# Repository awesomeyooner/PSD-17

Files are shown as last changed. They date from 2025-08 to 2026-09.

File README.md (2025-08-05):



# PSD-17

The PSD-21 is an FOC controller designed for stepper motors, specifically for NEMA 17 stepper motors.

Click here for the [manual](./docs/Manual.md)
## Folder Tree

```bash
.
├── esp_test_firmware # Test firmware on ESP32
│   └── firmware # PlatformIO Project
├── firmware # Main firmware (SAMD21)
├── i2c_test # I2C Master Communication Test
│   └── project  # CMake Project
├── pcb # KiCad Project
├── samd21_test_firmware # Test firmware on SAMD21
│   └── firmware # PlatformIO Project
└── README.md
```

## Hardware Details

- [NEMA 17 Motor](https://www.omc-stepperonline.com/nema-17-stepper-motor)
    - [STEPPERONLINE 23mm](https://www.amazon.com/dp/B0B93PNYCP?ref=ppx_yo2ov_dt_b_fed_asin_title&th=1)
    - [STEPPERONLINE 38mm](https://www.amazon.com/dp/B0B38GX54H?ref=ppx_yo2ov_dt_b_fed_asin_title&th=1)
- [AS5047P Magnetic Encoder](https://www.digikey.com/en/products/detail/ams-osram-usa-inc/AS5047P-ADAPTERBOARD/5452344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)
    - [Diametric Magnet](https://www.digikey.com/en/products/detail/radial-magnets-inc/9049/6030786) (6mm x 2.5mm )
- [DRV8874 DC Motor Driver](https://www.pololu.com/product/4035) (2x)
- [SAMD21 Seeed Studio Xiao](https://www.amazon.com/Seeeduino-Smallest-Microcontroller-Interfaces-Compatible/dp/B08745JBRP?th=1)

### Passive Components 

- [5V Voltage Regulator](https://www.pololu.com/product/5433?gQT=1)

## Datasheets

### AS5047P
- [Board](https://www.mouser.com/datasheet/2/588/AS5047P-TS_EK_AB_Operation-Manual_Rev.1.0-775823.pdf)
- [Chip](https://look.ams-osram.com/m/d05ee39221f9857/original/AS5047P-DS000324.pdf)

### DRV8874
- [Board](https://www.pololu.com/product/4035)
- [Chip](https://www.ti.com/lit/ds/symlink/drv8874.pdf)

### SAMD21
- [Seeed Studio Xiao](https://wiki.seeedstudio.com/Seeeduino-XIAO/)
- [SAMD21 Chip](https://ww1.microchip.com/downloads/en/DeviceDoc/SAM_D21_DA1_Family_DataSheet_DS40001882F.pdf)

### NEMA 17
- [23mm](https://www.omc-stepperonline.com/e-series-nema-17-bipolar-1-8deg-17ncm-24-07oz-in-1a-42x42x23mm-4-wires-17he08-1004s)
- [38mm](https://www.omc-stepperonline.com/e-series-nema-17-bipolar-42ncm-59-49oz-in-1-5a-42x42x38mm-4-wires-w-1m-cable-connector-17he15-1504s)

## Contact
Feel free to reach out!
- awesomeyooner@gmail.com

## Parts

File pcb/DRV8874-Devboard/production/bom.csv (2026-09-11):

Designator | Footprint | Quantity | Value | LCSC Part #
C1, C7 | 0402 | 2 | 22nF | C1532
C10 | 0603 | 1 | 10uF | C96446
C11, C14, C15, C16, C17, C18, C19, C2, C5, C8, C9 | 0402 | 11 | 100nF | C307331
C12 | 1206 | 1 | 4.7uF | C29823
C13 | 0603 | 1 | 33pF | C1663
C3, C6 | CP_Elec_10x10.5 | 2 | 330uF | C46550419
C4 | 0603 | 1 | 33nF | C21117
D1, D3, D4, D5 | LED_WS2812B-2020_PLCC4_2.0x2.0mm | 4 | WS2812B-2020 | C3646929
D2 | D_SMA | 1 | D_Schottky | C2480
J1, J5 | PinHeader_1x04_P2.54mm_Vertical | 2 | Conn_01x04_Pin
J10, J11 | PinHeader_1x06_P2.54mm_Vertical | 2 | Conn_01x06_Pin
J12, J3, J4, J6, J7, J8, J9 | PinHeader_1x03_P2.54mm_Vertical | 7 | Conn_01x03_Pin
J13, J14 | PinHeader_1x02_P2.54mm_Vertical | 2 | Conn_01x02_Pin
J2 | CONN-TH_2P-P5.08_DB128L-5.08-2P-BK-S | 1 | Screw_Terminal_01x02 | C430601
L2 | 1008 | 1 | 4u7 | C5832360
R1, R19 | 0402 | 2 | 2k2 | C25879
R10, R15, R18 | 0603 | 3 | 20k | C4184
R11 | 0603 | 1 | 124k | C22788
R12 | 0603 | 1 | 23k7 | C2933175
R13, R16 | 0603 | 2 | 15k | C22809
R14, R17 | 0603 | 2 | 75k | C23242
R2, R21, R6 | 0402 | 3 | 10k | C25744
R22, R9 | 0603 | 2 | 100k | C25803
R23 | 0402 | 1 | 470 | C25117
R3 | 0402 | 1 | 120 | C25079
R5 | 0603 | 1 | 3k | C4211
R7 | 0603 | 1 | 18k | C25810
R8 | 0603 | 1 | 510k | C23192
U1, U3 | HTSSOP-16-1EP_4.4x5mm_P0.65mm_EP3.4x5mm_Mask2.46x2.31mm | 2 | DRV8874 | C1855818
U2 | SOT-23-6 | 1 | BL9342 | C93176
U4 | SOIC-8_3.9x4.9mm_P1.27mm | 1 | SN65HVD230 | C12084
U5 | HTSSOP20_PWP_TEX | 1 | TPS16630PWPR | C1849461
U6 | SO-8_3.9x4.9mm_P1.27mm | 1 | M95320-WMN6TP | C283459
U7 | TinyThinker_HAT | 1 | TinyThinker_J1 | C1525

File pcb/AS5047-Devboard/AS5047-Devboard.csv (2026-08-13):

Comment | Designator | JLCPCB Part # | Footprint | Qty | DNP
1uF | C1 | C15849 | Capacitor_SMD:C_0603_1608Metric | 1
MountingHole | H1,H2,H3,H4 |  | MountingHole:MountingHole_3.2mm_M3 | 4 | DNP
SPI_CONN | J1 |  | Connector_PinHeader_2.54mm:PinHeader_1x06_P2.54mm_Vertical | 1 | DNP
AS5047P | U1 | C962063 | Package_SO:TSSOP-14_4.4x5mm_P0.65mm | 1

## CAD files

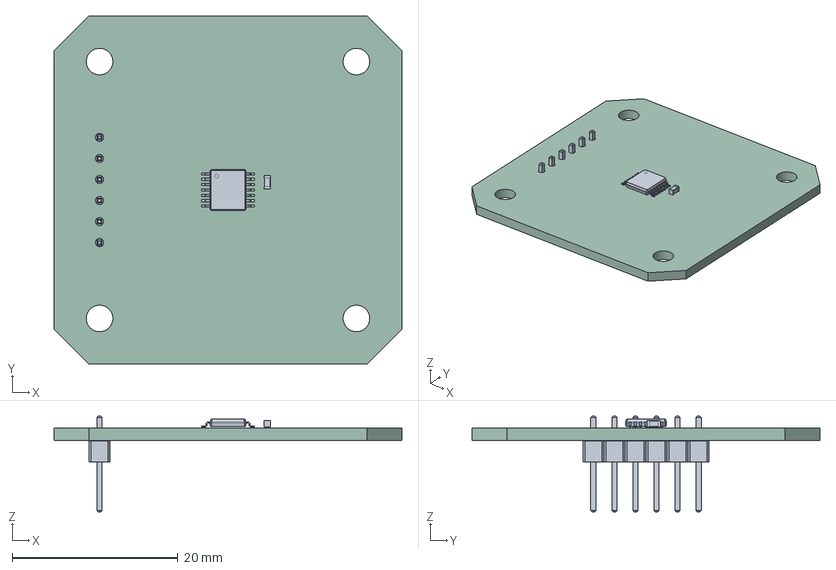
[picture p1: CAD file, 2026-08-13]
pcb/AS5047-Devboard/AS5047-Devboard.step
42.0 x 42.0 x 11.5 mm
TSSOP-14_4.4x5mm_P0.65mm
C_0603_1608Metric
PinHeader_1x06_P2.54mm_Vertical
AS5047-Devboard_PCB

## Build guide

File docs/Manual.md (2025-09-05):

# Manual for PSD 17

## I2C Communication

| Byte 1 | Byte 2... Byte N |
| --- | --- |
| Data Type | Data |

> **NOTE** Data Length is the number of bytes for the `data` section, so it does not include the first byte

### Commands 
| Data Types | Byte Value | Data Length (to send) |
| :---: | :---: | :---: |
| Disable Motor Command | 0 | 0 |
| Enable Motor Command | 1 | 0 |
| Run FOC Init | 2 | 0 |
| Target Command | 3 | 4 (float) |
| Closed Loop Velocity Command | 4 | 4 (float) |  
| Closed Loop Position Command | 5 | 4 (float) |
| Closed Loop Torque Command | 6 | 4 (float) |
| Open Loop Velocity Command | 7 | 4 (float) |
| ... | ... | ... |

### Settings 

> **NOTE** For Torque Modes, 0 is `Voltage`, 1 is `DC Current`, 2 is `FOC Current`

| Data Types | Byte Value | Data Length (to send) |
| :---: | :---: | :---: |
| Change Motor Current Limit | 121 | 4 (float) |
| Change Motor Phase Resistance | 122 | 4 (float) |
| Change Motor Voltage Alignment | 123 | 4 (float) |
| Change Motor Voltage Limit | 124 | 4 (float) |
| Change Driver Voltage Limit | 125 | 4 (float) |
| Change Supply Voltage | 126 | 4 (float) |
| Change Torque Mode | 127 | 4 (float) | 
| Velocity kP | 128 | 4 (float) |
| Velocity kI | 129 | 4 (float) |
| Velocity kD | 130 | 4 (float) |
| Position kP | 131 | 4 (float) |
| Position kI | 132 | 4 (float) |
| Position kD | 133 | 4 (float) |
| Position kF | 134 | 4 (float) |
| Current q kP | 135 | 4 (float) |
| Current q kI | 136 | 4 (float) |
| Current q kD | 137 | 4 (float) |
| Current d kP | 138 | 4 (float) |
| Current d kI | 139 | 4 (float) |
| Current d kD | 140 | 4 (float) |

### Requests

> **NOTE** Data Length is the number of bytes for the `data` section to be recieved, it will send back the first byte as an acknowledgement check

| Data Types | Byte Value | Data Length (to recieve) |
| :---: | :---: | :---: |
| Target Request | 255 | 4 (float) |
| Velocity Request | 254 | 4 (float) |
| Position Request | 253 |  4 (float) |
| Current Request | 252 | 4 (float) |
| Error Request | 251 | 1 (uint8_t) |
| Is Enabled | 250 | 4 (float) |
| ... | ... | ... |

#### Error Codes

> **NOTE** None exist yet

| Byte Value | Error Type |
| :---: | :---: |
| ... | ... |

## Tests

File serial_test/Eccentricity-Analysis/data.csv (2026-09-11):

Time (seconds) | Residual
3.370819 | -0.009212208603
3.384102 | -0.005275901659
3.397432 | -0.002451066113
3.410817 | -0.0003394630535
3.424124 | 0.004959560623
3.437419 | 0.006142725934
3.450883 | 0.00938481324
3.464132 | 0.01149835481
3.477477 | 0.01232976332
3.490828 | 0.011198601
3.504183 | 0.008137058147
3.517492 | 0.005073891551
3.530823 | -0.0002273680388
3.544168 | -0.002326959535
3.557462 | -0.003710699088
3.570818 | -0.002625337081
3.584126 | -0.0005344085405
3.597495 | -0.00001428330302
3.61091 | 0.002816465673
3.624185 | 0.003975533706
3.637513 | 0.006538559524
3.650915 | 0.00466754527
3.664214 | 0.007084330035
3.677534 | 0.005172116943
3.690906 | 0.001651956772
3.704192 | -0.001949021693
3.717504 | -0.005691473697
3.730915 | -0.009966344176
3.744173 | -0.01215365883
3.757516 | -0.009370060053
3.770909 | -0.008503218082
3.784191 | -0.005576816003
3.797513 | -0.002691219368
3.810911 | -0.0008208530775
3.824192 | 0.003132644138
3.837533 | 0.005149433187
3.850909 | 0.008015892472
3.864216 | 0.008296916149
3.877631 | 0.007816665125
3.890947 | 0.003554832576
3.904263 | -0.0002939999719
3.917674 | -0.004004870451
3.93107 | -0.007407313889
3.944339 | -0.00770167504
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

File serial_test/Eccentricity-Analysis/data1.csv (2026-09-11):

Time (seconds) | Residual | Normalized Residual
10.360027 | -0.008153365409 | -0.001240810441
10.373313 | -0.00875378085 | -0.001332183967
10.386668 | -0.008027601053 | -0.001221671139
10.400011 | -0.005670568254 | -0.000862968841
10.413354 | -0.004043535455 | -0.000615360745
10.426786 | -0.003035329088 | -0.0004619280305
10.439957 | -0.002170069927 | -0.0003302495703
10.453334 | -0.0003054539669 | -0.00004648515704
10.466663 | 0.002101574001 | 0.0003198255975
10.479952 | 0.003526445309 | 0.0005366679819
10.493296 | 0.005033907025 | 0.0007660792915
10.506751 | 0.003747978471 | 0.0005703817487
10.520002 | 0.002025550952 | 0.0003082561181
10.533362 | 0.001087875332 | 0.0001655570433
10.546669 | -0.002849532863 | -0.0004336528479
10.559957 | -0.005003090472 | -0.0007613895102
10.573358 | -0.009272180516 | -0.001411076018
10.586656 | -0.009631448959 | -0.001465750869
10.599999 | -0.008198416161 | -0.001247666437
10.613338 | -0.007841099028 | -0.001193288545
10.626754 | -0.006708755325 | -0.001020964134
10.640055 | -0.004345737019 | -0.0006613509387
10.653394 | -0.0004754198854 | -0.00007235122287
10.666769 | 0.003707338241 | 0.0005641969626
10.680093 | 0.004776221627 | 0.0007268637387
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

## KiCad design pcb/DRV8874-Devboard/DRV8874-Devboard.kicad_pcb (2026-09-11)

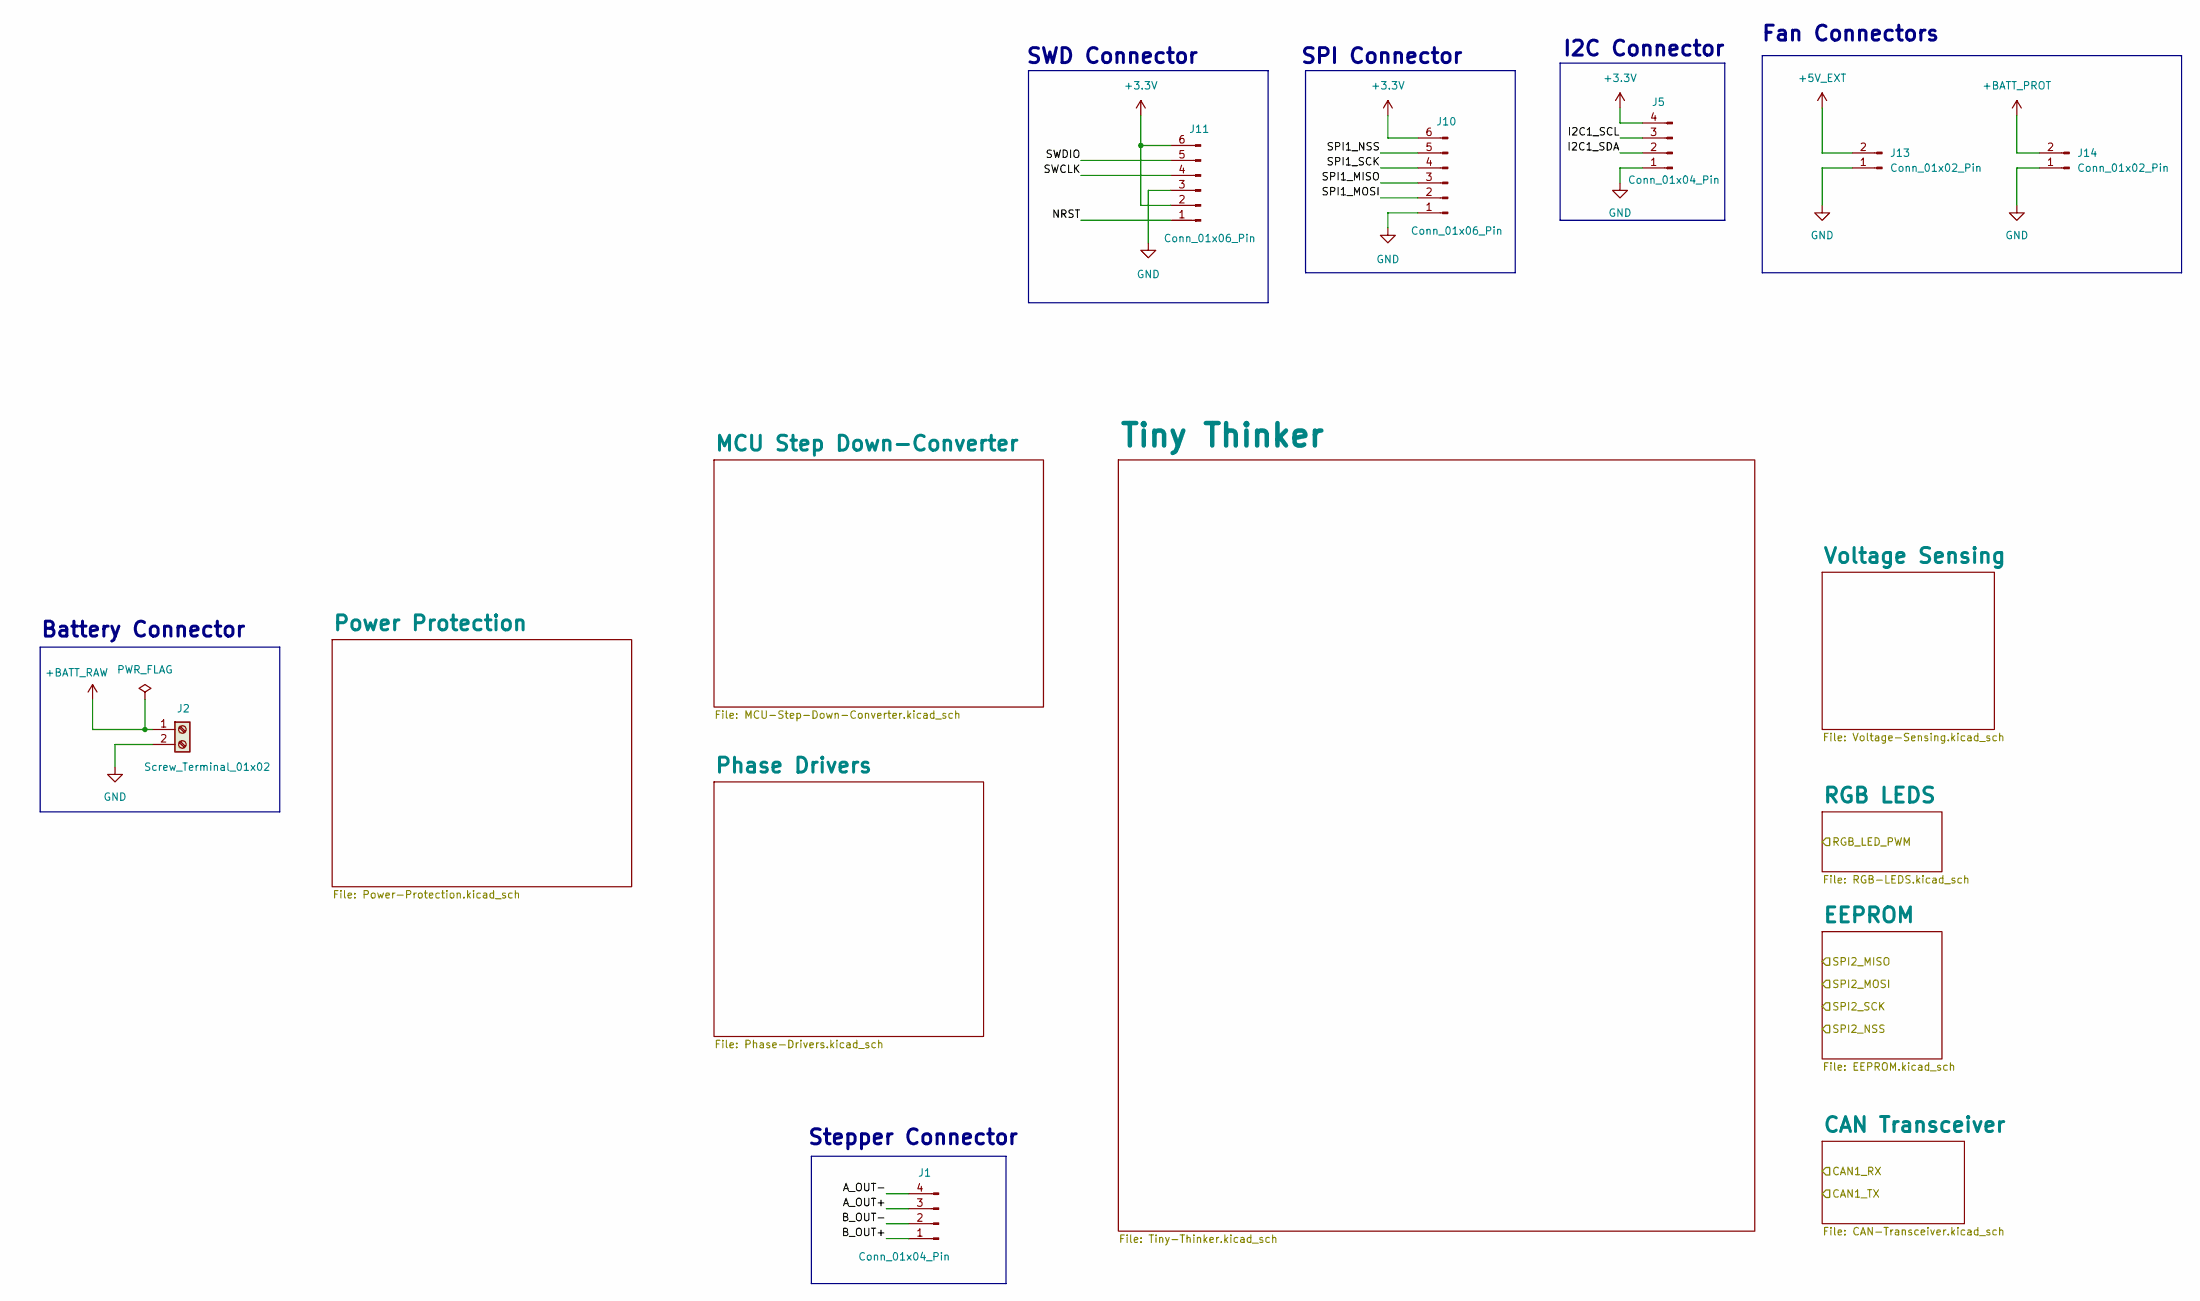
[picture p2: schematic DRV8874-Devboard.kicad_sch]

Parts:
J1, J5: Conn_01x04_Pin; PinHeader_1x04_P2.54mm_Vertical
J2: Screw_Terminal_01x02; CONN-TH_2P-P5.08_DB128L-5.08-2P-BK-S; JLCPCB Part # C430601
J10, J11: Conn_01x06_Pin; PinHeader_1x06_P2.54mm_Vertical
J13, J14: Conn_01x02_Pin; PinHeader_1x02_P2.54mm_Vertical

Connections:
+3.3V: J5.4, J10.6, J11.2, J11.6; also elsewhere on the board
+5V_EXT: J13.2; also elsewhere on the board
+BATT_PROT: J14.2; also elsewhere on the board
+BATT_RAW: J2.1; also elsewhere on the board
/A_OUT+: J1.3
/A_OUT-: J1.4
/B_OUT+: J1.1
/B_OUT-: J1.2
/I2C1_SCL: J5.3
/I2C1_SDA: J5.2
/NRST: J11.1
/SPI1_MISO: J10.3
/SPI1_MOSI: J10.2
/SPI1_NSS: J10.5
/SPI1_SCK: J10.4
/SWCLK: J11.4
/SWDIO: J11.5
GND: J2.2, J5.1, J10.1, J11.3, J13.1, J14.1; also elsewhere on the board

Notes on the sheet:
SWD Connector
Fan Connectors
Battery Connector
SPI Connector
Stepper Connector
I2C Connector

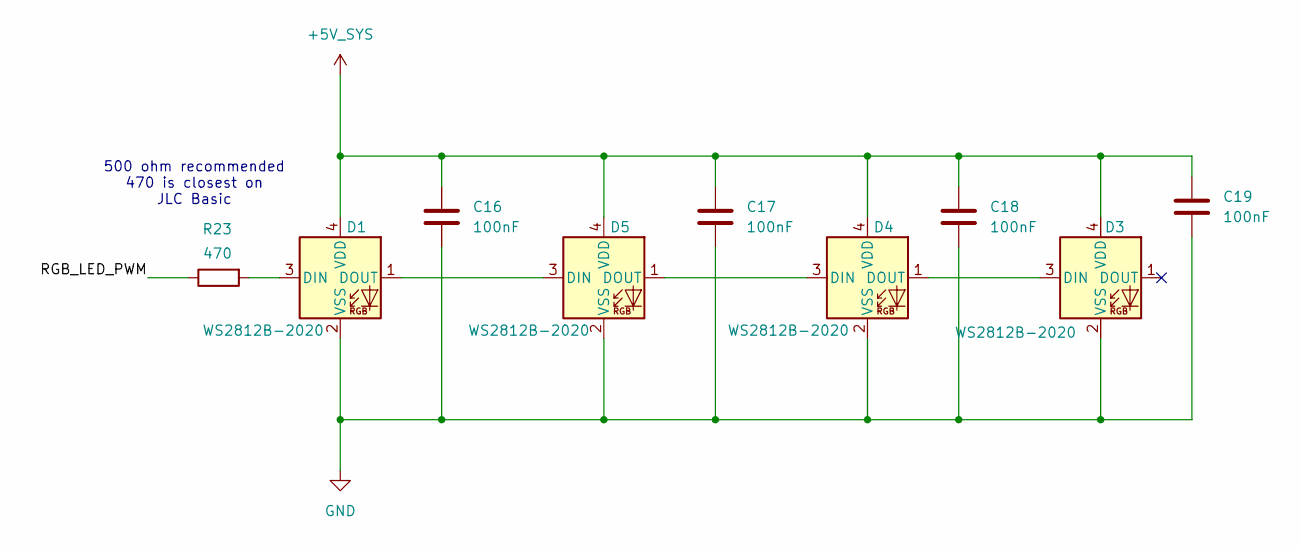
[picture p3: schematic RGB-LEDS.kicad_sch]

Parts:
C16, C17, C18, C19: 100nF; C_0402_1005Metric; JLCPCB Part # C307331
D1, D3, D4, D5: WS2812B-2020; LED_WS2812B-2020_PLCC4_2.0x2.0mm; JLCPCB Part # C3646929
R23: 470; R_0402_1005Metric; JLCPCB Part # C25117

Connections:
+5V_SYS: C16.1, C17.1, C18.1, C19.1, D1.4 (VDD), D3.4 (VDD), D4.4 (VDD), D5.4 (VDD); also elsewhere on the board
/RGB LEDS/RGB_LED_PWM: R23.1
GND: C16.2, C17.2, C18.2, C19.2, D1.2 (VSS), D3.2 (VSS), D4.2 (VSS), D5.2 (VSS); also elsewhere on the board
unnamed: D1.3 (DIN), R23.2
unnamed: D1.1 (DOUT), D5.3 (DIN)
unnamed: D3.3 (DIN), D4.1 (DOUT)
unnamed: D4.3 (DIN), D5.1 (DOUT)

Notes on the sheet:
500 ohm recommended 470 is closest on JLC Basic

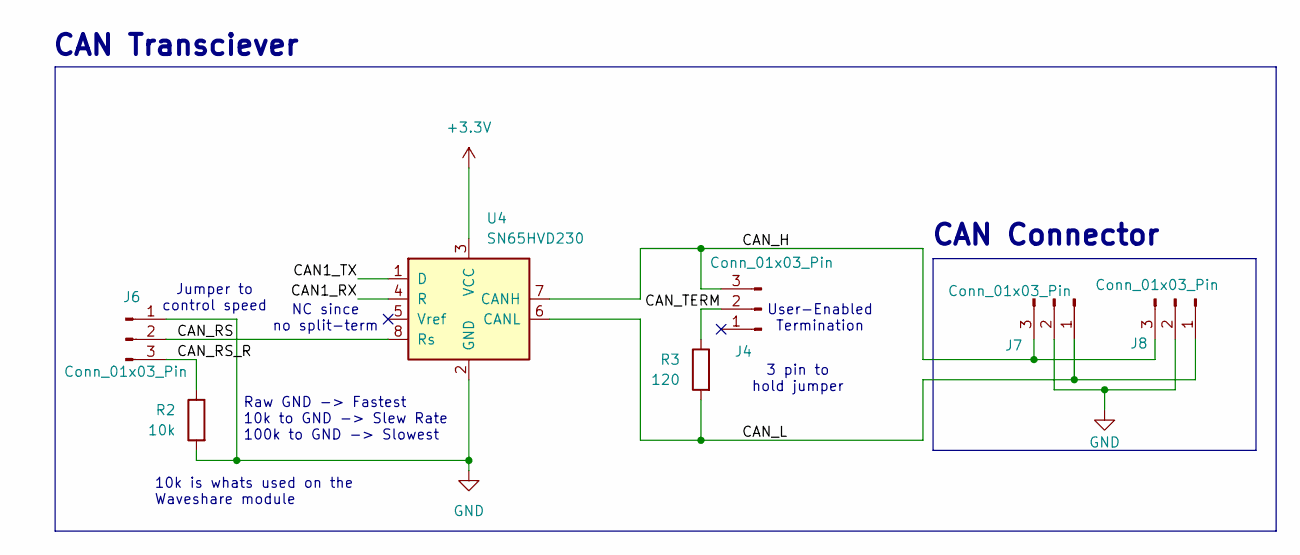
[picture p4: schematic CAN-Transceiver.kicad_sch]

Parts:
J4, J6, J7, J8: Conn_01x03_Pin; PinHeader_1x03_P2.54mm_Vertical
R2: 10k; R_0402_1005Metric; JLCPCB Part # C25744
R3: 120; R_0402_1005Metric; JLCPCB Part # C25079
U4: SN65HVD230; SOIC-8_3.9x4.9mm_P1.27mm; JLCPCB Part # C12084

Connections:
+3.3V: U4.3 (VCC); also elsewhere on the board
/CAN Transceiver/CAN1_RX: U4.4 (R)
/CAN Transceiver/CAN1_TX: U4.1 (D)
/CAN Transceiver/CAN_H: J4.3, J7.3, J8.3, U4.7 (CANH)
/CAN Transceiver/CAN_L: J7.1, J8.1, R3.2, U4.6 (CANL)
/CAN Transceiver/CAN_RS: J6.2, U4.8 (Rs)
/CAN Transceiver/CAN_RS_R: J6.3, R2.1
/CAN Transceiver/CAN_TERM: J4.2, R3.1
GND: J6.1, J7.2, J8.2, R2.2, U4.2 (GND); also elsewhere on the board

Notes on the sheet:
Jumper to control speed
10k is whats used on the Waveshare module
CAN Connector
CAN Transciever
Raw GND -> Fastest 10k to GND -> Slew Rate 100k to GND -> Slowest
3 pin to hold jumper
User-Enabled Termination
NC since no split-term

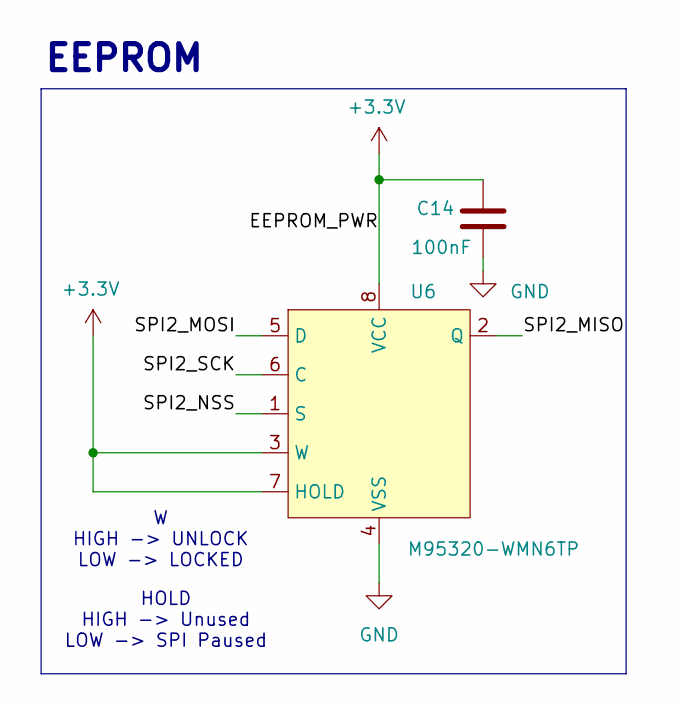
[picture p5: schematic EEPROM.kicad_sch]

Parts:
C14: 100nF; C_0402_1005Metric; JLCPCB Part # C307331
U6: M95320-WMN6TP; SO-8_3.9x4.9mm_P1.27mm; JLCPCB Part # C283459

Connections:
+3.3V: C14.1, U6.3 (W), U6.7 (HOLD), U6.8 (VCC); also elsewhere on the board
/EEPROM/SPI2_MISO: U6.2 (Q)
/EEPROM/SPI2_MOSI: U6.5 (D)
/EEPROM/SPI2_NSS: U6.1 (S)
/EEPROM/SPI2_SCK: U6.6 (C)
GND: C14.2, U6.4 (VSS); also elsewhere on the board

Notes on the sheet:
HOLD HIGH -> Unused LOW -> SPI Paused
EEPROM
W HIGH -> UNLOCK LOW -> LOCKED

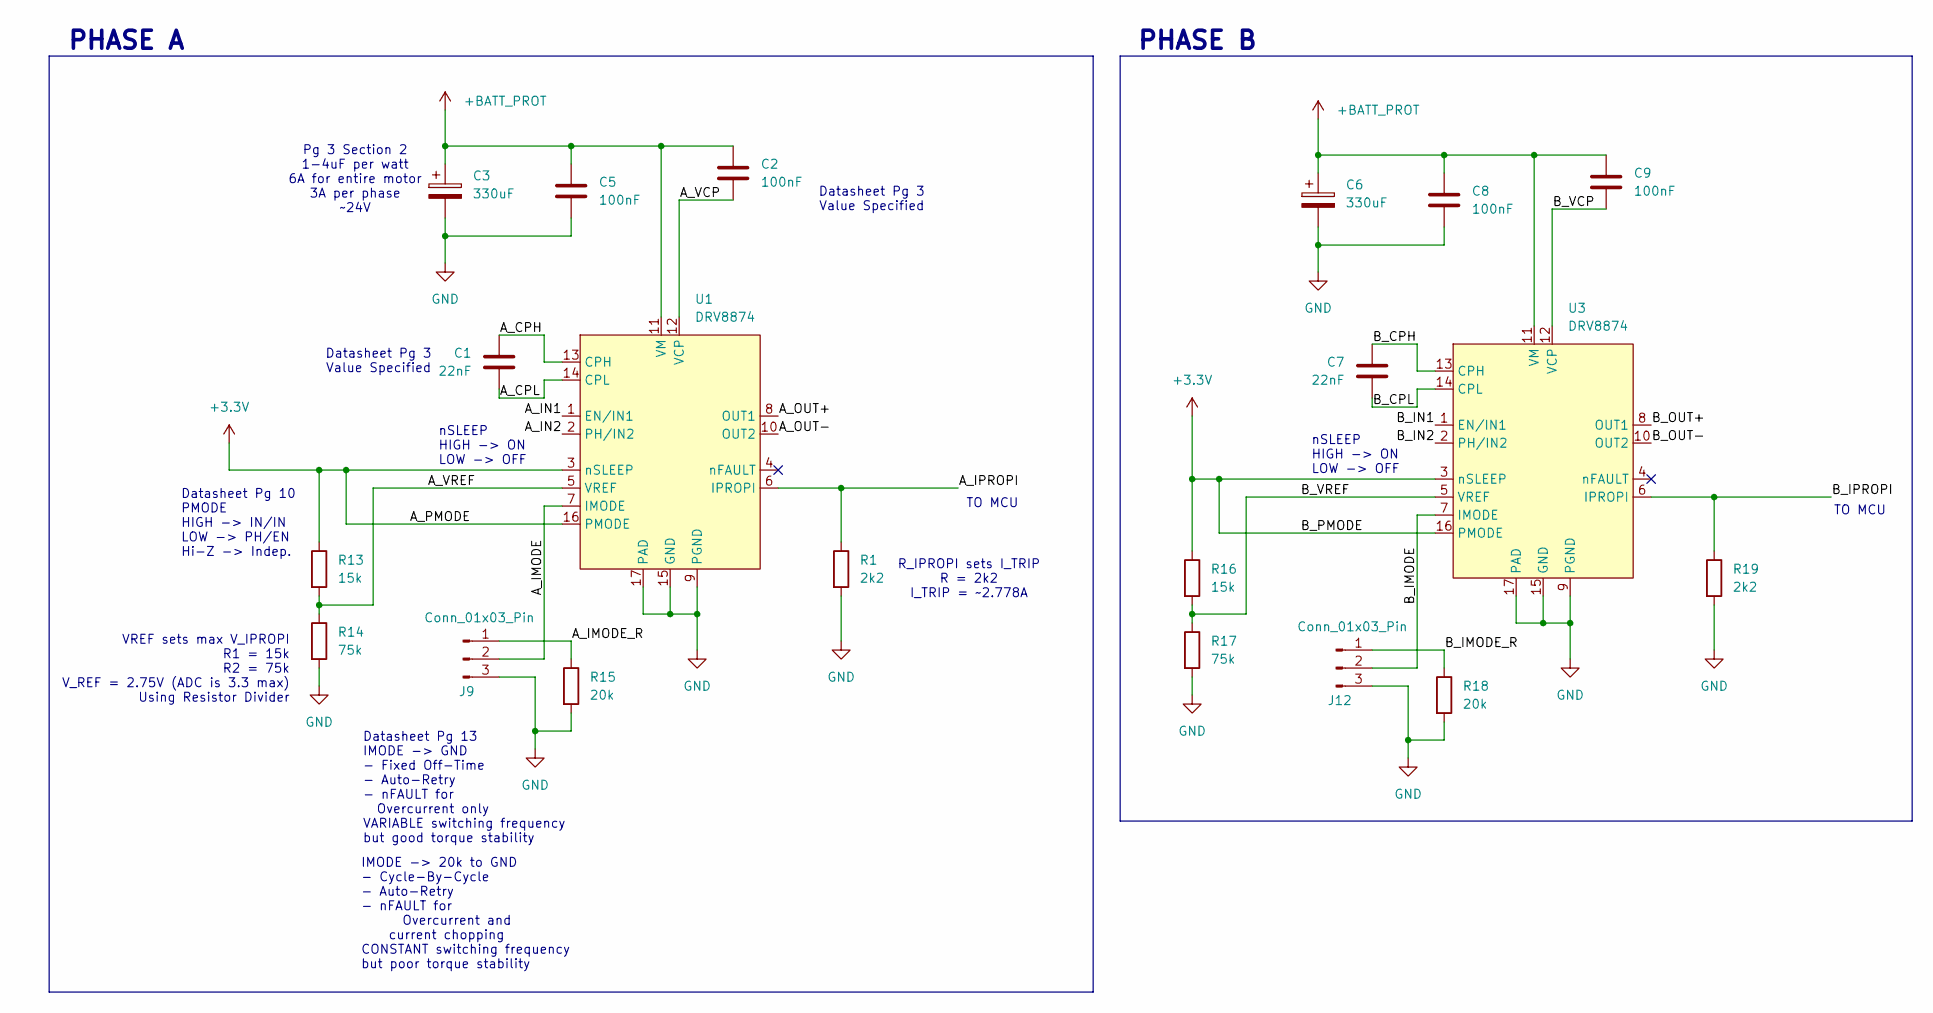
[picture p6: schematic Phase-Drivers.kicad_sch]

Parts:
C1, C7: 22nF; C_0402_1005Metric; JLCPCB Part # C1532
C2, C5, C8, C9: 100nF; C_0402_1005Metric; JLCPCB Part # C307331
C3, C6: 330uF; CP_Elec_10x10.5; JLCPCB Part # C46550419
J9, J12: Conn_01x03_Pin; PinHeader_1x03_P2.54mm_Vertical
R1, R19: 2k2; R_0402_1005Metric; JLCPCB Part # C25879
R13, R16: 15k; R_0603_1608Metric; JLCPCB Part # C22809
R14, R17: 75k; R_0603_1608Metric; JLCPCB Part # C23242
R15, R18: 20k; R_0603_1608Metric; JLCPCB Part # C4184
U1, U3: DRV8874; HTSSOP-16-1EP_4.4x5mm_P0.65mm_EP3.4x5mm_Mask2.46x2.31mm; JLCPCB Part # C1855818

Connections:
+3.3V: R13.1, R16.1, U1.3 (nSLEEP), U1.16 (PMODE), U3.3 (nSLEEP), U3.16 (PMODE); also elsewhere on the board
+BATT_PROT: C2.1, C3.1, C5.1, C6.1, C8.1, C9.1, U1.11 (VM), U3.11 (VM); also elsewhere on the board
/Phase Drivers/A_CPH: C1.1, U1.13 (CPH)
/Phase Drivers/A_CPL: C1.2, U1.14 (CPL)
/Phase Drivers/A_IMODE: J9.2, U1.7 (IMODE)
/Phase Drivers/A_IMODE_R: J9.1, R15.1
/Phase Drivers/A_IN1: U1.1 (EN/IN1)
/Phase Drivers/A_IN2: U1.2 (PH/IN2)
/Phase Drivers/A_IPROPI: R1.1, U1.6 (IPROPI)
/Phase Drivers/A_OUT+: U1.8 (OUT1)
/Phase Drivers/A_OUT-: U1.10 (OUT2)
/Phase Drivers/A_VCP: C2.2, U1.12 (VCP)
/Phase Drivers/A_VREF: R13.2, R14.1, U1.5 (VREF)
/Phase Drivers/B_CPH: C7.1, U3.13 (CPH)
/Phase Drivers/B_CPL: C7.2, U3.14 (CPL)
/Phase Drivers/B_IMODE: J12.2, U3.7 (IMODE)
/Phase Drivers/B_IMODE_R: J12.1, R18.1
/Phase Drivers/B_IN1: U3.1 (EN/IN1)
/Phase Drivers/B_IN2: U3.2 (PH/IN2)
/Phase Drivers/B_IPROPI: R19.1, U3.6 (IPROPI)
/Phase Drivers/B_OUT+: U3.8 (OUT1)
/Phase Drivers/B_OUT-: U3.10 (OUT2)
/Phase Drivers/B_VCP: C9.2, U3.12 (VCP)
/Phase Drivers/B_VREF: R16.2, R17.1, U3.5 (VREF)
GND: C3.2, C5.2, C6.2, C8.2, J9.3, J12.3, R1.2, R14.2, R15.2, R17.2, R18.2, R19.2, U1.9 (PGND), U1.15 (GND), U1.17 (PAD), U3.9 (PGND), U3.15 (GND), U3.17 (PAD); also elsewhere on the board

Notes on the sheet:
Datasheet Pg 3 Value Specified
PHASE B
Datasheet Pg 13 IMODE -> GND - Fixed Off-Time - Auto-Retry - nFAULT for Overcurrent only VARIABLE switching frequency but good torque stability
PHASE A
nSLEEP HIGH -> ON LOW -> OFF
VREF sets max V_IPROPI R1 = 15k R2 = 75k V_REF = 2.75V (ADC is 3.3 max) Using Resistor Divider
TO MCU
IMODE -> 20k to GND - Cycle-By-Cycle - Auto-Retry - nFAULT for Overcurrent and current chopping CONSTANT switching frequency but poor torque stability
Pg 3 Section 2 1-4uF per watt 6A for entire motor 3A per phase ~24V
R_IPROPI sets I_TRIP R = 2k2 I_TRIP = ~2.778A
Datasheet Pg 10 PMODE HIGH -> IN/IN LOW -> PH/EN Hi-Z -> Indep.

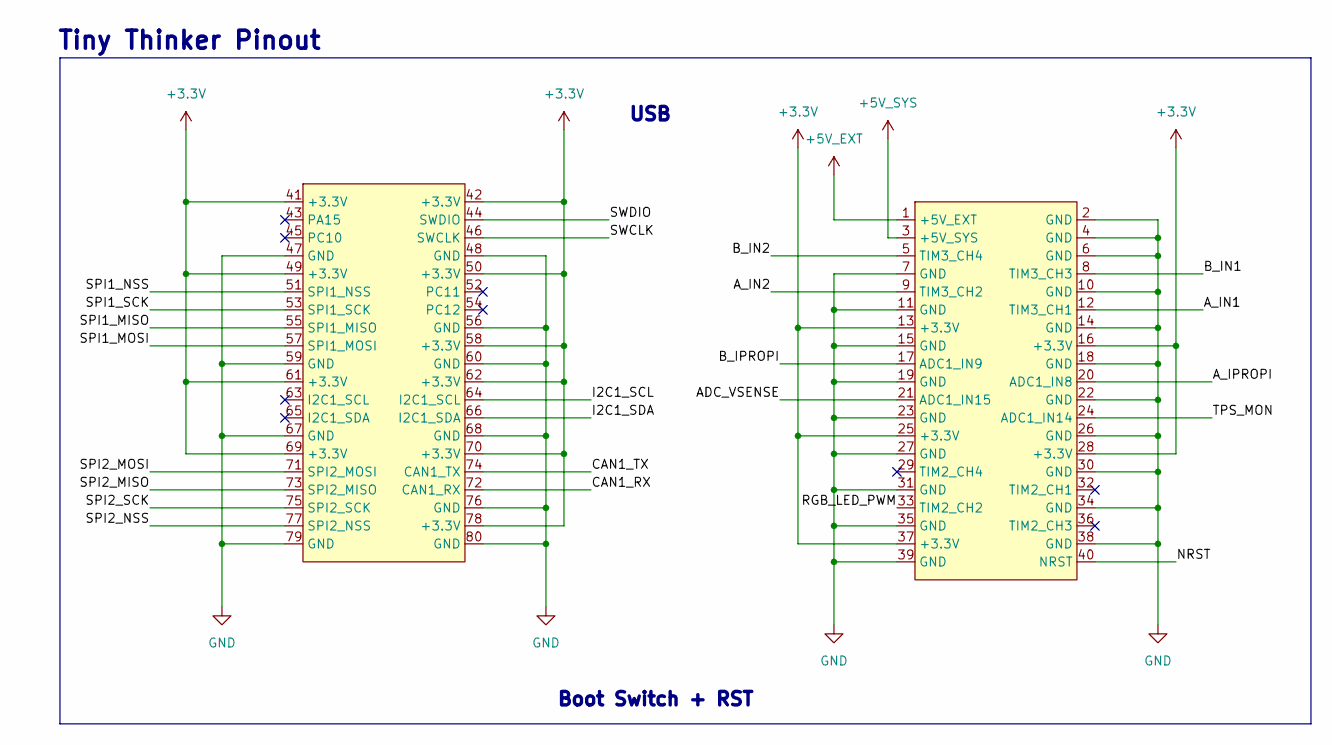
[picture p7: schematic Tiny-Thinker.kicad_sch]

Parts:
U7: TinyThinker_J1; TinyThinker_HAT

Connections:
+3.3V: U7.13 (+3.3V), U7.16 (+3.3V), U7.25 (+3.3V), U7.28 (+3.3V), U7.37 (+3.3V), U7.41 (+3.3V), U7.42 (+3.3V), U7.49 (+3.3V), U7.50 (+3.3V), U7.58 (+3.3V), U7.61 (+3.3V), U7.62 (+3.3V), U7.69 (+3.3V), U7.70 (+3.3V), U7.78 (+3.3V); also elsewhere on the board
+5V_EXT: U7.1 (+5V_EXT); also elsewhere on the board
+5V_SYS: U7.3 (+5V_SYS); also elsewhere on the board
/Tiny Thinker/ADC_VSENSE: U7.21 (ADC1_IN15)
/Tiny Thinker/A_IN1: U7.12 (TIM3_CH1)
/Tiny Thinker/A_IN2: U7.9 (TIM3_CH2)
/Tiny Thinker/A_IPROPI: U7.20 (ADC1_IN8)
/Tiny Thinker/B_IN1: U7.8 (TIM3_CH3)
/Tiny Thinker/B_IN2: U7.5 (TIM3_CH4)
/Tiny Thinker/B_IPROPI: U7.17 (ADC1_IN9)
/Tiny Thinker/CAN1_RX: U7.72 (CAN1_RX)
/Tiny Thinker/CAN1_TX: U7.74 (CAN1_TX)
/Tiny Thinker/I2C1_SCL: U7.64 (I2C1_SCL)
/Tiny Thinker/I2C1_SDA: U7.66 (I2C1_SDA)
/Tiny Thinker/NRST: U7.40 (NRST)
/Tiny Thinker/RGB_LED_PWM: U7.33 (TIM2_CH2)
/Tiny Thinker/SPI1_MISO: U7.55 (SPI1_MISO)
/Tiny Thinker/SPI1_MOSI: U7.57 (SPI1_MOSI)
/Tiny Thinker/SPI1_NSS: U7.51 (SPI1_NSS)
/Tiny Thinker/SPI1_SCK: U7.53 (SPI1_SCK)
/Tiny Thinker/SPI2_MISO: U7.73 (SPI2_MISO)
/Tiny Thinker/SPI2_MOSI: U7.71 (SPI2_MOSI)
/Tiny Thinker/SPI2_NSS: U7.77 (SPI2_NSS)
/Tiny Thinker/SPI2_SCK: U7.75 (SPI2_SCK)
/Tiny Thinker/SWCLK: U7.46 (SWCLK)
/Tiny Thinker/SWDIO: U7.44 (SWDIO)
/Tiny Thinker/TPS_MON: U7.24 (ADC1_IN14)
GND: U7.2 (GND), U7.4 (GND), U7.6 (GND), U7.7 (GND), U7.10 (GND), U7.11 (GND), U7.14 (GND), U7.15 (GND), U7.18 (GND), U7.19 (GND), U7.22 (GND), U7.23 (GND), U7.26 (GND), U7.27 (GND), U7.30 (GND), U7.31 (GND), U7.34 (GND), U7.35 (GND), U7.38 (GND), U7.39 (GND), U7.47 (GND), U7.48 (GND), U7.56 (GND), U7.59 (GND), U7.60 (GND), U7.67 (GND), U7.68 (GND), U7.76 (GND), U7.79 (GND), U7.80 (GND); also elsewhere on the board

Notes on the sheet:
Tiny Thinker Pinout
Boot Switch + RST
USB

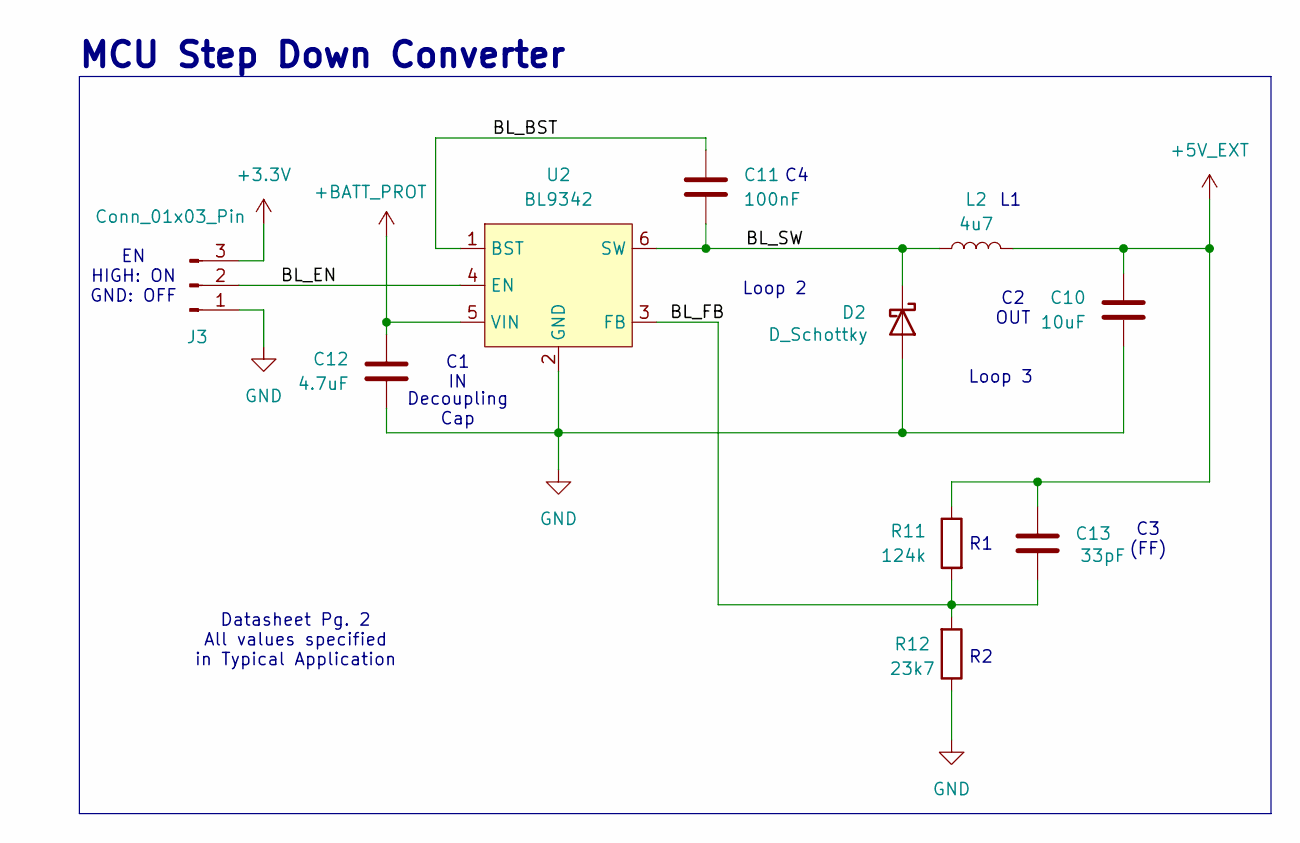
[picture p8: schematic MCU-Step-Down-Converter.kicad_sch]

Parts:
C10: 10uF; C_0603_1608Metric; JLCPCB Part # C96446
C11: 100nF; C_0402_1005Metric; JLCPCB Part # C307331
C12: 4.7uF; C_1206_3216Metric; JLCPCB Part # C29823
C13: 33pF; C_0603_1608Metric; JLCPCB Part # C1663
D2: D_Schottky; D_SMA; JLCPCB Part # C2480
J3: Conn_01x03_Pin; PinHeader_1x03_P2.54mm_Vertical
L2: 4u7; L_1008_2520Metric; JLCPCB Part # C5832360
R11: 124k; R_0603_1608Metric; JLCPCB Part # C22788
R12: 23k7; R_0603_1608Metric; JLCPCB Part # C2933175
U2: BL9342; SOT-23-6; JLCPCB Part # C93176

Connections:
+3.3V: J3.3; also elsewhere on the board
+5V_EXT: C10.1, C13.2, L2.2, R11.1; also elsewhere on the board
+BATT_PROT: C12.1, U2.5 (VIN); also elsewhere on the board
/MCU Step Down-Converter/BL_BST: C11.1, U2.1 (BST)
/MCU Step Down-Converter/BL_EN: J3.2, U2.4 (EN)
/MCU Step Down-Converter/BL_FB: C13.1, R11.2, R12.2, U2.3 (FB)
/MCU Step Down-Converter/BL_SW: C11.2, D2.1 (K), L2.1, U2.6 (SW)
GND: C10.2, C12.2, D2.2 (A), J3.1, R12.1, U2.2 (GND); also elsewhere on the board

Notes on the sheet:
MCU Step Down Converter
C2 OUT
Datasheet Pg. 2 All values specified in Typical Application
C3 (FF)
Loop 3
Decoupling Cap
Loop 2
EN HIGH: ON GND: OFF
C1 IN

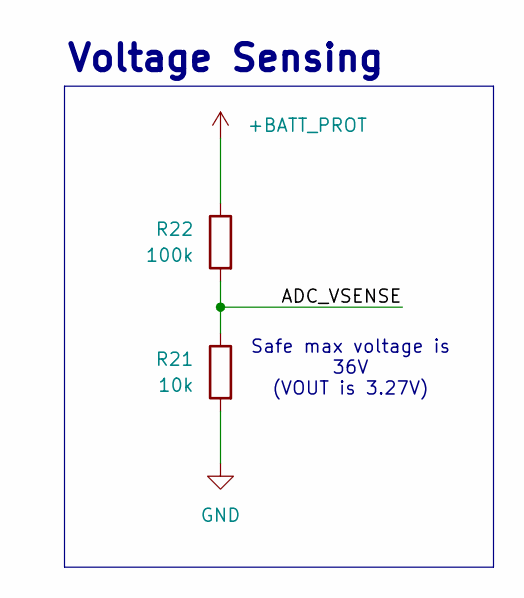
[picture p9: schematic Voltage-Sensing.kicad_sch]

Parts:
R21: 10k; R_0402_1005Metric; JLCPCB Part # C25744
R22: 100k; R_0603_1608Metric; JLCPCB Part # C25803

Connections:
+BATT_PROT: R22.1; also elsewhere on the board
/Voltage Sensing/ADC_VSENSE: R21.1, R22.2
GND: R21.2; also elsewhere on the board

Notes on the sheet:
Voltage Sensing
Safe max voltage is 36V (VOUT is 3.27V)

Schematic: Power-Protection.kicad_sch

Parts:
C4: 33nF; C_0603_1608Metric; JLCPCB Part # C21117
C15: 100nF; C_0402_1005Metric; JLCPCB Part # C307331
R5: 3k; R_0603_1608Metric; JLCPCB Part # C4211
R6: 10k; R_0402_1005Metric; JLCPCB Part # C25744
R7: 18k; R_0603_1608Metric; JLCPCB Part # C25810
R8: 510k; R_0603_1608Metric; JLCPCB Part # C23192
R9: 100k; R_0603_1608Metric; JLCPCB Part # C25803
R10: 20k; R_0603_1608Metric; JLCPCB Part # C4184
U5: TPS16630PWPR; HTSSOP20_PWP_TEX; JLCPCB Part # C1849461

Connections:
+3.3V: R6.1, U5.13 (*SHDN); also elsewhere on the board
+BATT_PROT: U5.18 (OUT), U5.19 (OUT), U5.20 (OUT); also elsewhere on the board
+BATT_RAW: C15.2, R8.1, U5.1 (IN), U5.2 (IN), U5.3 (IN), U5.6 (P_IN); also elsewhere on the board
/Power Protection/TPS_DVDT: C4.1, U5.10 (DVDT)
/Power Protection/TPS_FLT: R6.2, U5.15 (*FLT)
/Power Protection/TPS_ILIM: R5.1, U5.11 (ILIM)
/Power Protection/TPS_MON: R7.1, U5.14 (IMON)
/Power Protection/TPS_OVP: R9.2, R10.1, U5.8 (OVP)
/Power Protection/TPS_UVLO: R8.2, R9.1, U5.7 (UVLO)
GND: C4.2, C15.1, R5.2, R7.2, R10.2, U5.9 (GND), U5.12 (MODE), U5.21 (GND); also elsewhere on the board

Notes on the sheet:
Power Protection
IMON 18k ~3V @ 6A
MODE -> GND Auto-Retry
to STM32
33nF => 1A ~15ms
UVLO ~6V OVP ~38V
Datasheet Pg 28 9.2.2.2 R's Calc
Max V: 36V Min V: 6V (for DRV8874)
FLT HIGH: Norm LOW: Fault
SHDN HIGH: ON GND: OFF
100nF Decoupling Cap
I_OL = 6A

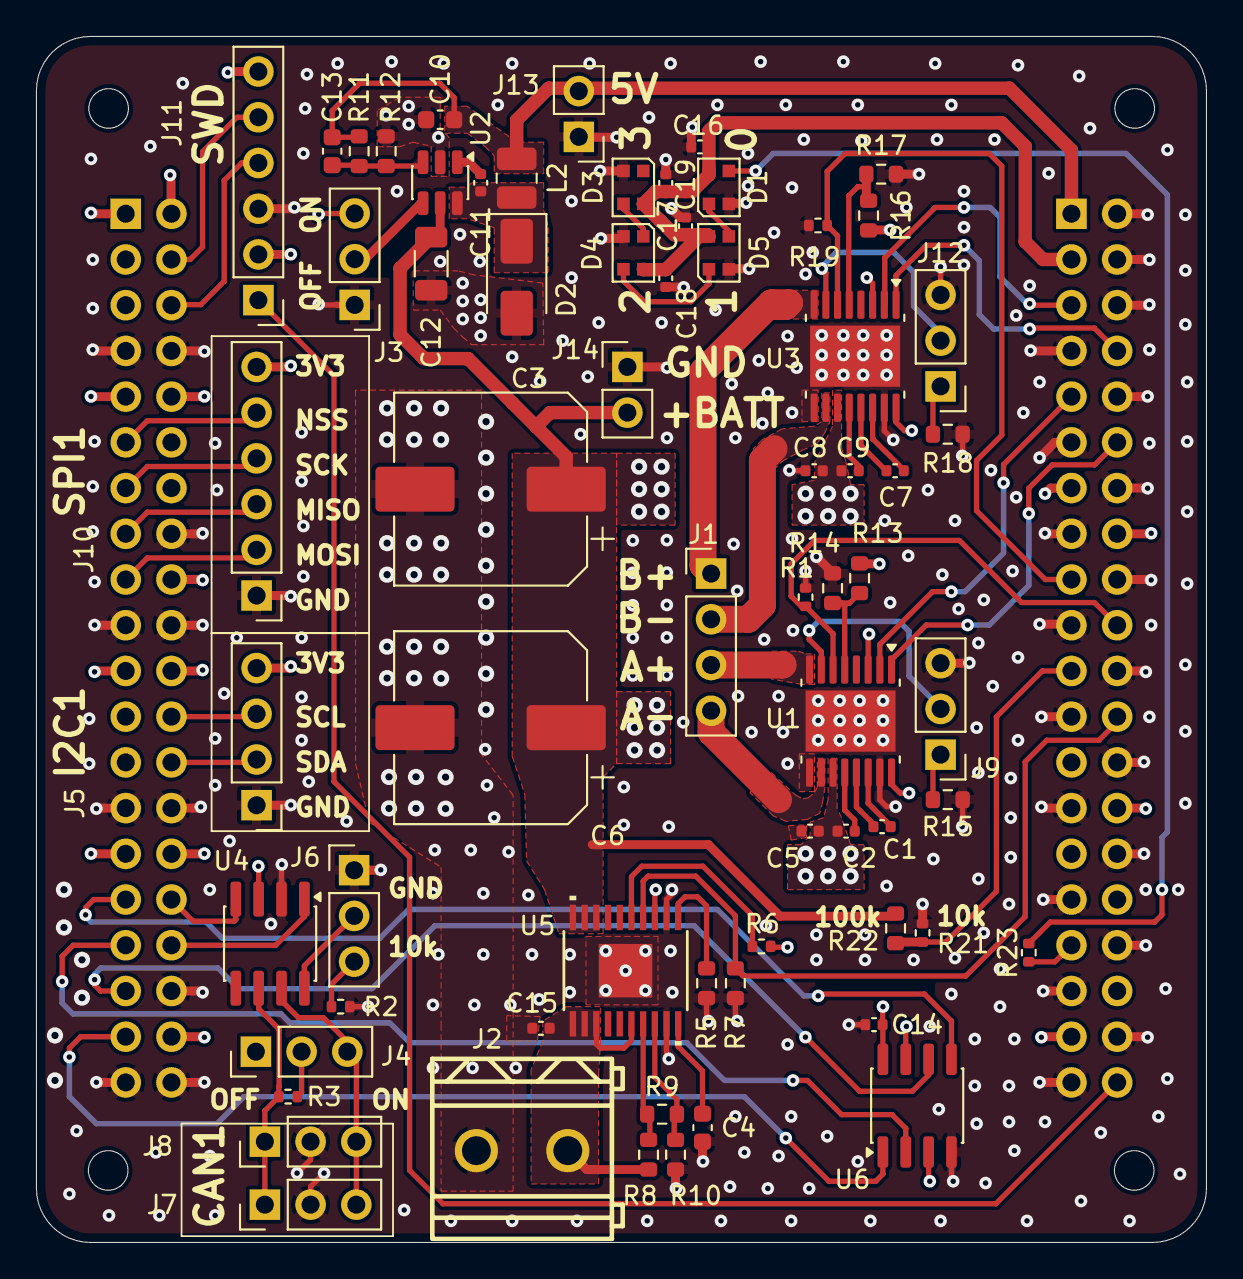
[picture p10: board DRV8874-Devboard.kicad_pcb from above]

Board: 4 copper layers, 65.0 x 67.0 mm, 67 parts (1 on the bottom side), 40 nets.

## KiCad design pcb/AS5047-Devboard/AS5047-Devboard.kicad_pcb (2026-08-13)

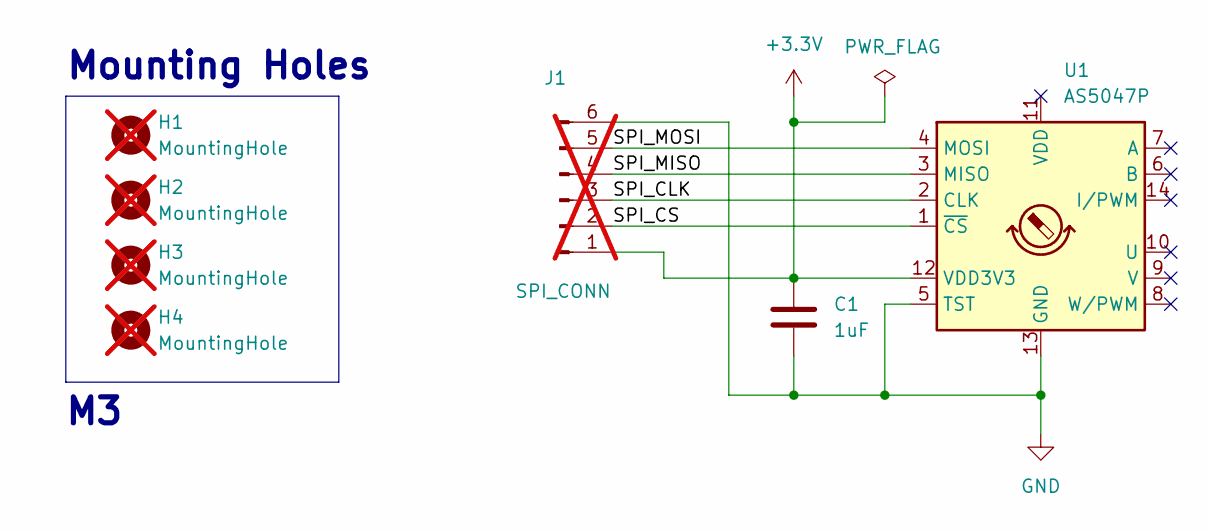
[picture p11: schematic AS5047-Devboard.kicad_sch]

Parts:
C1: 1uF; C_0603_1608Metric; JLCPCB Part # C15849
H1, H2, H3, H4: MountingHole; MountingHole_3.2mm_M3; not fitted
J1: SPI_CONN; PinHeader_1x06_P2.54mm_Vertical; not fitted
U1: AS5047P; TSSOP-14_4.4x5mm_P0.65mm; JLCPCB Part # C962063

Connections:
+3.3V: C1.1, J1.1, U1.12 (VDD3V3)
/SPI_CLK: J1.3, U1.2 (CLK)
/SPI_CS: J1.2, U1.1 (~CS)
/SPI_MISO: J1.4, U1.3 (MISO)
/SPI_MOSI: J1.5, U1.4 (MOSI)
GND: C1.2, J1.6, U1.5 (TST), U1.13 (GND)

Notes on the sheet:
Mounting Holes

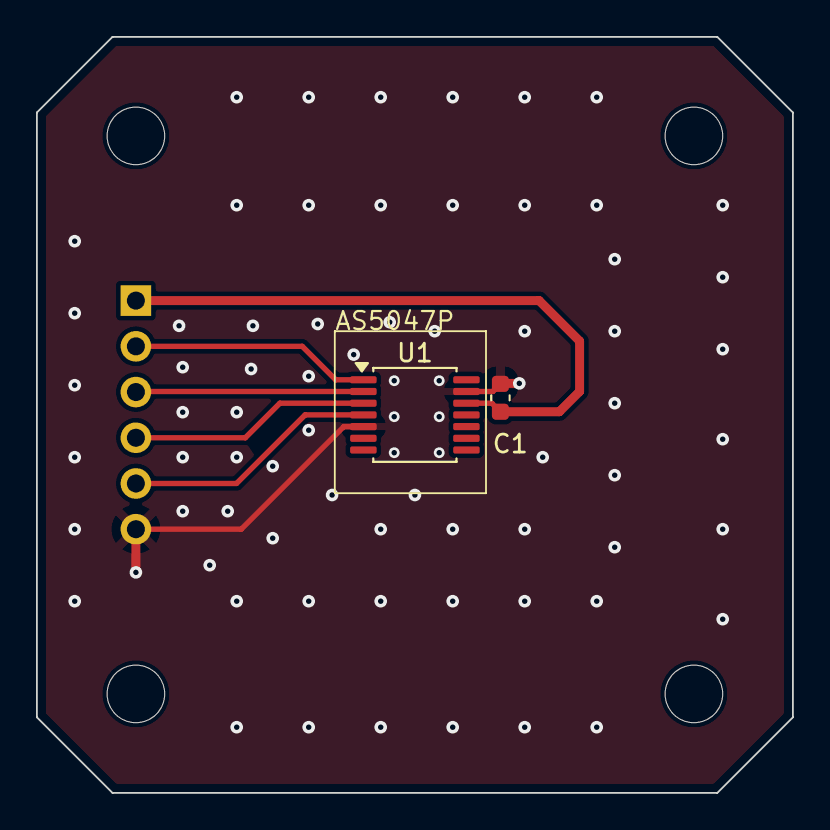
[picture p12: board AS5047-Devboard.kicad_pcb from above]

Board: 2 copper layers, 42.0 x 42.0 mm, 7 parts (1 on the bottom side), 6 nets.

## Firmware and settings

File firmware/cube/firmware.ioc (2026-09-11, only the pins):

Mcu.UserName=STM32F446RCTx
PA1.Signal=S_TIM2_CH2
PA11.Signal=USB_OTG_FS_DM
PA12.Signal=USB_OTG_FS_DP
PA13.Signal=SYS_JTMS-SWDIO
PA14.Signal=SYS_JTCK-SWCLK
PA9.Signal=USB_OTG_FS_VBUS
PB0.Signal=ADCx_IN8
PB1.Signal=ADCx_IN9
PB12.Signal=GPIO_Output
PB13.Signal=SPI2_SCK
PB14.Signal=SPI2_MISO
PB15.Signal=SPI2_MOSI
PB3.Signal=SPI1_SCK
PB4.Signal=SPI1_MISO
PB5.Signal=SPI1_MOSI
PC1.Signal=GPIO_Output
PC4.Signal=ADCx_IN14
PC5.Signal=ADCx_IN15
PC6.Signal=S_TIM8_CH1
PC7.Signal=S_TIM8_CH2
PC8.Signal=S_TIM8_CH3
PC9.Signal=S_TIM8_CH4
PD2.Signal=GPIO_Output
PH0-OSC_IN.Signal=RCC_OSC_IN
PH1-OSC_OUT.Signal=RCC_OSC_OUT

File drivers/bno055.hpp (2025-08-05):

#ifndef BNO055_HPP
#define BNO055_HPP

#include "i2c/i2c.h"

#include <string>
#include <iostream>
#include <string.h>
#include <functional>

#include "math/vector3d.hpp"
#include "math/math_helper.hpp"

#include "util.hpp"
#include "status.hpp"
#include <unistd.h>
#include <thread>

// Accelerometer
constexpr uint8_t REG_ACCEL_LSB_X = 0x08;
constexpr uint8_t REG_ACCEL_MSB_X = 0x09;

constexpr uint8_t REG_ACCEL_LSB_Y = 0x0A;
constexpr uint8_t REG_ACCEL_MSB_Y = 0x0B;

constexpr uint8_t REG_ACCEL_LSB_Z = 0x0C;
constexpr uint8_t REG_ACCEL_MSB_Z = 0x0D;

// Magnetometer
constexpr uint8_t REG_MAG_LSB_X = 0x0E;
constexpr uint8_t REG_MAG_MSB_X = 0x0F;

constexpr uint8_t REG_MAG_LSB_Y = 0x10;
constexpr uint8_t REG_MAG_MSB_Y = 0x11;

constexpr uint8_t REG_MAG_LSB_Z = 0x12;
constexpr uint8_t REG_MAG_MSB_Z = 0x13;

// Gyroscope
constexpr uint8_t REG_GYRO_LSB_X = 0x14;
constexpr uint8_t REG_GYRO_MSB_X = 0x15;

constexpr uint8_t REG_GYRO_LSB_Y = 0x16;
constexpr uint8_t REG_GYRO_MSB_Y = 0x17;

constexpr uint8_t REG_GYRO_LSB_Z = 0x18;
constexpr uint8_t REG_GYRO_MSB_Z = 0x19;

// Others
constexpr uint8_t REG_MODE = 0x3D;
constexpr uint8_t CONF_MODE = 0x00;
constexpr uint8_t AMG_MODE = 0x07;

using namespace math_util;
class BNO055{

    public:

        BNO055(){}

        StatusCode run_ack(std::function<StatusCode(void)> runnable, int attempts, std::string prefix = "", double delay = 1.0){

            for(int i = 1; i < attempts + 1; i++){
                StatusCode status = runnable();
                usleep(conversions::seconds_to_micros(delay));

                if(status == StatusCode::OK){

                    if(prefix.length() != 0)
                        print(prefix + " OK!");
                        
                    return StatusCode::OK;
                }
                else if(status == StatusCode::FAILED && i != attempts){

                    if(prefix.length() != 0)
                        print(prefix + " FAILED! Retrying...");

                }
                else{

                    if(prefix.length() != 0)
                        print(prefix + " FAILED! Ending...");

                    return StatusCode::FAILED;
                }
            }
        }

        StatusCode init(const char* name = "/dev/i2c-9", unsigned short address = 0x28){
            device.addr = address;

            bus = i2c_open(name);

            device.addr = address;
            device.bus = bus;
            device.iaddr_bytes = 1;
            device.page_bytes = 1;

            if(bus == -1)
                return StatusCode::FAILED;
            else
                return StatusCode::OK;
        }

        StatusCode set_mode_AMG(){
            write_bus(REG_MODE, CONF_MODE);
            usleep(conversions::seconds_to_micros(0.5));
            return write_bus(REG_MODE, AMG_MODE);
        }


        void init_threads(){
            // std::thread accel_thread(
            //     [this](){
            //         while(true){
            //             accel = get_accel();
            //         }
            //     }
            // );

            // std::thread gyro_thread(
            //     [this](){
            //         while(true){
            //             gyro = get_gyro();
            //         }
            //     }
            // );

            // std::thread mag_thread(
            //     [this](){
            //         while(true){
            //             mag = get_mag();
            //         }
            //     }
            // );

            std::thread refresh_thread(
                [this](){
                    while(true){
                        if(refresh_all() != StatusCode::OK)
                            print("FAILED!");
                    }
                }
            );

            std::thread print_thread(
                [this](){
                    while(true){
                        std::cout << "Accel: \t" + accel.to_string() + "\t";
                        std::cout << "Gyro: \t" + gyro.to_string() + "\t";
                        std::cout << "Mag: \t" + mag.to_string() << std::endl;
                    }
                }
            );
                
            

            // accel_thread.join();
            // gyro_thread.join();
            // mag_thread.join();
            refresh_thread.join();
            print_thread.join();
        }

        void close(){
            i2c_close(bus);
        }

        StatusCode refresh_all(){
            uint8_t data[18];

            StatusCode status = i2c_read(&device, 0x08, data, sizeof(data)) == sizeof(data) ? StatusCode::OK : StatusCode::FAILED;

            int16_t raw_accel_x = (data[1] << 8) | data[0];
            int16_t raw_accel_y = (data[3] << 8) | data[2];
            int16_t raw_accel_z = (data[5] << 8) | data[4];

            int16_t raw_mag_x = (data[7] << 8) | data[6];
            int16_t raw_mag_y = (data[9] << 8) | data[8];
            int16_t raw_mag_z = (data[11] << 8) | data[10];

            int16_t raw_gyro_x = (data[13] << 8) | data[12];
            int16_t raw_gyro_y = (data[15] << 8) | data[14];
            int16_t raw_gyro_z = (data[17] << 8) | data[16];

            double accel_x = conversions::mg_to_mps2((double)(raw_accel_x));
            double accel_y = conversions::mg_to_mps2((double)(raw_accel_y));
            double accel_z = conversions::mg_to_mps2((double)(raw_accel_z));

            accel.refresh(accel_x, accel_y, accel_z);

            double mag_x = (double)(raw_mag_x) / 1000.0;
            double mag_y = (double)(raw_mag_y) / 1000.0;
            double mag_z = (double)(raw_mag_z) / 1000.0;

            mag.refresh(mag_x, mag_y, mag_z);

            double gyro_x = conversions::degrees_to_radians((double)(raw_gyro_x));
            double gyro_y = conversions::degrees_to_radians((double)(raw_gyro_y));
            double gyro_z = conversions::degrees_to_radians((double)(raw_gyro_z));

            gyro.refresh(gyro_x, gyro_y, gyro_z);

            return status;
        }

        StatusCode refresh_accel(){
            StatusedValue<double> x = get_reading(REG_ACCEL_LSB_X, REG_ACCEL_MSB_X);
            StatusedValue<double> y = get_reading(REG_ACCEL_LSB_Y, REG_ACCEL_MSB_Y);
            StatusedValue<double> z = get_reading(REG_ACCEL_LSB_Z, REG_ACCEL_MSB_Z);

            accel.refresh(
                conversions::mg_to_mps2(x.value),
                conversions::mg_to_mps2(y.value),
                conversions::mg_to_mps2(z.value)
            );

            return statuses_OK({x.status, y.status, z.status}) ? StatusCode::OK : StatusCode::FAILED;
        }

        StatusCode refresh_mag(){
            StatusedValue<double> x = get_reading(REG_MAG_LSB_X, REG_MAG_MSB_X);
            StatusedValue<double> y = get_reading(REG_MAG_LSB_Y, REG_MAG_MSB_Y);
            StatusedValue<double> z = get_reading(REG_MAG_LSB_Z, REG_MAG_MSB_Z);
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

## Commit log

2025-07-17 added initial kicad project
    [pcb.kicad_pcb, pcb.kicad_sch]
2025-08-04 updated readme to include more motors
2025-08-05 added wrapper class for i2c_device
2025-08-06 added spi sensor
2025-08-06 switched pins
2025-08-08 added dedicated AS5047 driver
2025-08-09 added esp32 firmware
2025-08-11 used static led
2025-08-12 switched firmware samd21 -> esp32
2025-08-12 added i2c test for esp32
2025-08-15 added i2c test
2025-08-23 added i2c test samd21 and esp32
2025-08-23 added lines to disable i2c pullup resistors on esp32
2025-08-23 added frequency changes to esp32
2025-08-28 added stm32 nucelo tests
2025-08-28 working foc example for stm32
2025-09-04 changed main firmware to be stm32f446re instead of esp32
2025-09-04 first test of i2c protol
2025-09-04 added abstraction for foc motor
2025-09-04 fixed sensor 0 issue
    [main.cpp]
2025-09-04 testing i2c
2025-09-04 added driver for master side
2025-09-30 changed current method to FOCCurrent
2025-10-06 swapped current pins for phase A and B and also added sensor offset + predetermined zero electric angle (skips alignemtn)
2025-10-06 added seperate threads for input, plotting, and main communication
2025-10-16 changed pins to allow for timer synchronization
2025-10-16 testing otu different currents
2025-10-16 added auto calibration
2025-12-03 added adc sampling time
2025-12-03 added initial schematic for protoboard
    [protoboard.kicad_pcb, protoboard.kicad_sch]
2025-12-03 added components
    [protoboard.kicad_sch]
2025-12-04 finished schematic for protoboard
2025-12-04 added more schematics
    [protoboard.kicad_sch]
2025-12-04 changed current
2025-12-05 added perfboard
    [protoboard.kicad_pcb, protoboard.kicad_sch]
2025-12-05 started perfboard layout
    [protoboard.kicad_pcb, protoboard.kicad_sch]
2025-12-26 changed spi variable
    [protoboard.kicad_pcb]
2025-12-26 changed CS pin
2025-12-31 updated schematic
2026-01-06 updated plib to use correct i2c path
2026-01-16 added testbench for stm32f446
2026-01-16 added custom file for AS5047 sensor
2026-02-13 Added AS5047 Devboard for NEMA17
    [AS5047-Devboard.kicad_pcb, AS5047-Devboard.kicad_sch]
2026-02-13 updated ground pour
    [AS5047-Devboard.kicad_pcb]
2026-02-13 DNP mounting holes
    [AS5047-Devboard-B_Cu.gbr, AS5047-Devboard-B_Mask.gbr, AS5047-Devboard-B_Paste.gbr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]
2026-02-13 unlocked file
    [AS5047-Devboard.kicad_pcb]
2026-02-17 added DRV8874 initial schematic
    [DRV8874-Devboard.kicad_pcb, DRV8874-Devboard.kicad_sch]
2026-02-22 moved AS5047 Devboard out one directory
    [AS5047-Devboard-B_Cu.gbr, AS5047-Devboard-B_Mask.gbr, AS5047-Devboard-B_Paste.gbr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]
2026-02-22 updated AS5047P board to include stitching vias
    [AS5047-Devboard.kicad_pcb]
2026-02-22 updated BOM
    [AS5047-Devboard-B_Cu.gbr, AS5047-Devboard-B_Mask.gbr, AS5047-Devboard-B_Paste.gbr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]
2026-02-23 added CAN transciever
    [DRV8874-Devboard.kicad_sch]
2026-02-24 exposed more connectors on DRV8874 devb
    [DRV8874-Devboard.kicad_sch]
2026-02-24 Updated sensor coorindates for AS5047P
    [AS5047-Devboard-B_Cu.gbr, AS5047-Devboard-B_Mask.gbr, AS5047-Devboard-B_Paste.gbr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]
2026-03-14 updated spi
2026-03-14 updated spi again
2026-03-14 spi finally works
2026-03-14 bruh I switched the silkscreen
    [AS5047-Devboard.kicad_pcb]
2026-03-17 started working on drv8874
    [DRV8874-Devboard.kicad_sch]
2026-03-26 minor changes to DRV8874
    [DRV8874-Devboard.kicad_sch]
2026-04-03 worked on DRV8874
    [DRV8874-Devboard.kicad_sch]
2026-04-04 started working on TPS16630
    [DRV8874-Devboard.kicad_sch]
2026-04-04 finished first iteration of TPS16630 implementation
    [DRV8874-Devboard.kicad_sch]
2026-04-05 updated DRV8874 to have tinythinker footprint
    [DRV8874-Devboard.kicad_sch]
2026-04-12 changed capacitor symbol to polarized
    [DRV8874-Devboard.kicad_sch]
2026-05-05 started working on BL9342
    [DRV8874-Devboard.kicad_sch]

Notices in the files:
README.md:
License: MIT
